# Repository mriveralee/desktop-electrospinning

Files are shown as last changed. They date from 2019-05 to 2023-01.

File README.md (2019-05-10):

# Research Code for Desktop Electrospinning

This is the research repository for `Desktop Electrospinning: A Single Extruder 3D Printer for Producing Rigid Plastic and Electrospun Textiles`. It contains the 3D printer firmware and control electronics set-up for the printer characterized in the publication  that can perform rigid plastic FDM 3D printer as well as melt electrospinning. [More information about the work can be found here](https://mikeriv.com/research/desktop-electrospinning/).

The [publication is also freely available here](https://mikeriv.com/assets/research/desktop-electrospinning/chi19-desktop-electrospinning.pdf).

  **NOTE: THIS PROJECT INVOLVES HIGH VOLTAGE -- BE AWARE AND USE AT YOUR OWN RISK!**
 

## 3D Printer Firmware and Control Electronics Set-up
This 3D printer uses a modified version of the Repeiter Firmware (v0.92) that includes add-ons for controlling high voltage via an infared signal. It also include firmware for two slave Arduino Nanos. One receives a high/low voltage signal from the 3D printer and sends out a corresponding an IR signal; the other Nano receives the IR signal and triggers a mechanical servo to open/close a connection to the high voltage ground on the 3D printer's build plate as well as toggle a solid-state relay that is connected to the high voltage power supply's AC-to-DC power adapter as shown in the simplified diagram below:

3D printer and melt electrospinning setup

## Hardware List
- High Voltage Power Supply, HV350REG(+), 5-35kV up to 1mA Positive (+) x 1 - [From Amazing1 Output](https://www.amazing1.com/hv-dc-power-supplies.html)
- Arduino Nano x 2 - [From Amazon](https://www.amazon.com/LAFVIN-Board-ATmega328P-Micro-Controller-Arduino/dp/B07G99NNXL/)
- IR Receiver Diode - can use [TSOP38238](https://www.sparkfun.com/products/10266)
- IR LED 950nm x 1 - [From Sparkfun](https://www.sparkfun.com/products/9349) 
- Servo S90 x 1 - [From Amazon](https://www.amazon.com/SunFounder-Digital-Helicopter-Fix-Wing-Airplane/dp/B01KZKOIZC/)
- Solid State Relay, 40A (3-32V DC Input) x 1 - [From Sparkfun](https://www.sparkfun.com/products/13015)
- Resistors - [From Amazon](https://www.amazon.com/AUSTOR-Resistors-Assortment-Resistor-Experiments/dp/B07BKRS4QZ/)
  - 330 Ohm Resistor x 1  
  - 470 Ohm Resistor x 3
- Servo - [From Amazon](https://www.amazon.com/SunFounder-Digital-Helicopter-Fix-Wing-Airplane/dp/B01KZKOIZC/)

The necessary electrical connections are shown in the circuit schematics below.

### IR Servo Switch Schematic
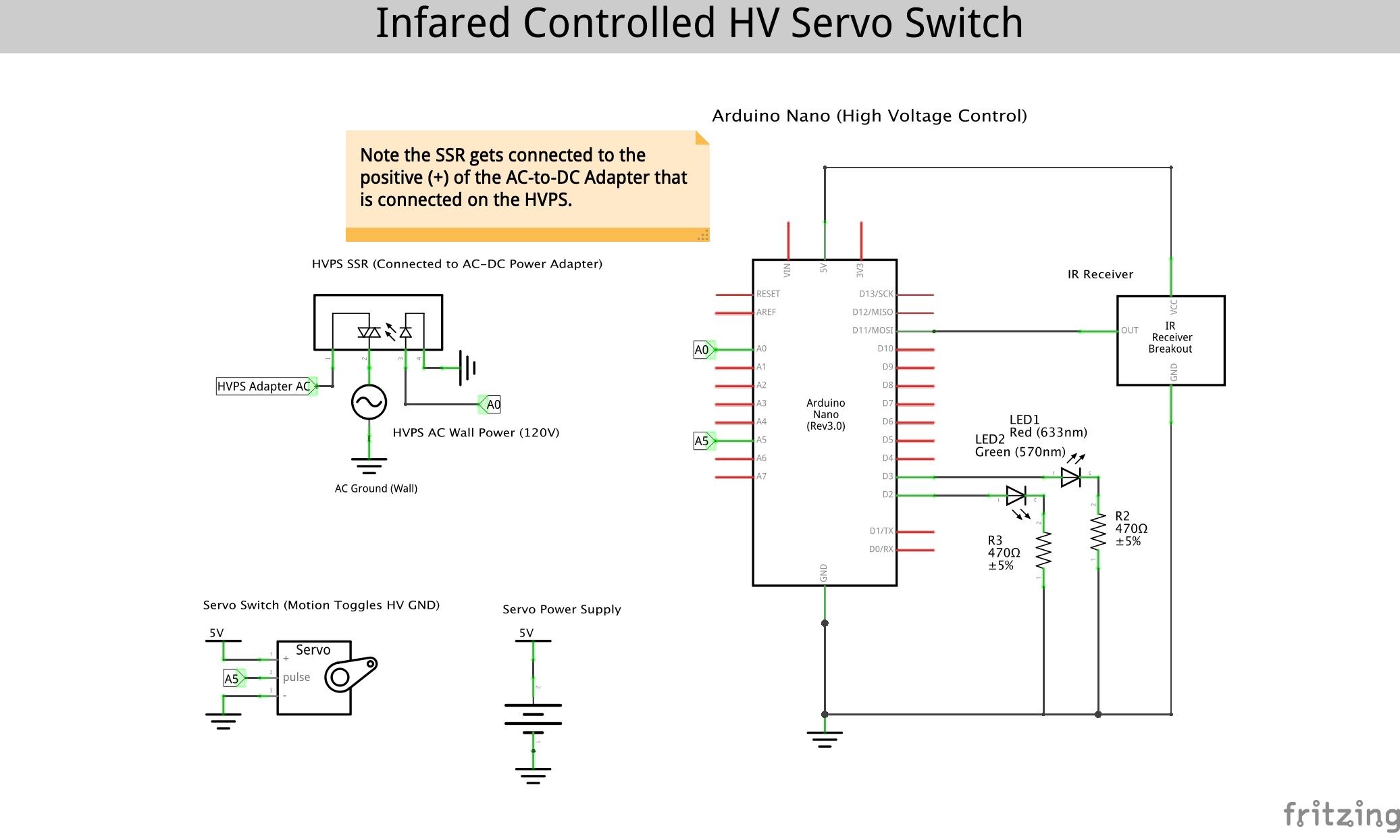
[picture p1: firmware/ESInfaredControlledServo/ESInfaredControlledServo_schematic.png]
irservo_schematic


### 3D Printer Slave IR Sender
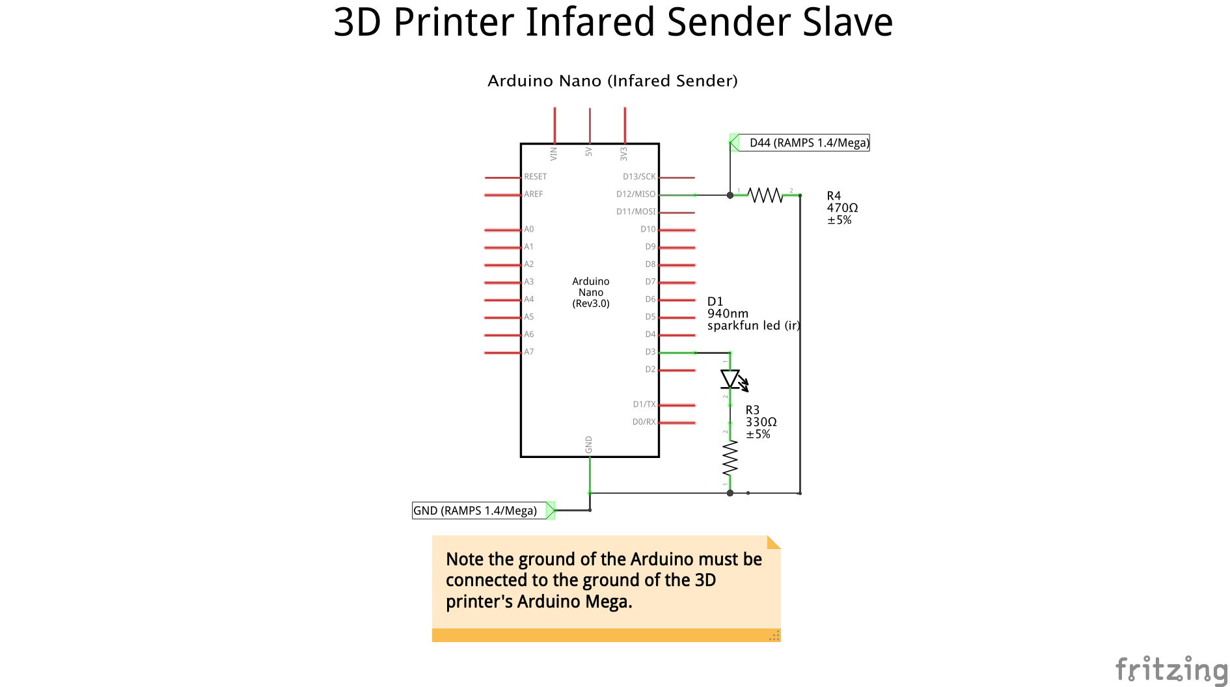
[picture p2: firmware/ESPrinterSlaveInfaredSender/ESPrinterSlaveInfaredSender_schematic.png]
irsender_schematic

Note: [RAMPS 1.4/Arduino Mega Pin out diagram can be found here](http://makerdev.com/blog/wp-content/uploads/2014/02/ramps_fanboard_annotations.jpg).

## Citation
Michael L. Rivera and Scott E. Hudson. 2019. Desktop Electrospinning: A Single Extruder 3D Printer for Producing Rigid Plastic and Electrospun Textiles. In CHI Conference on Human Factors in Computing Systems Proceedings (CHI 2019), May 4–9, 2019, Glasgow, Scotland UK. ACM, New York, NY, USA, 12 pages. https://doi.org/10.1145/3290605.3300434

# License
```MIT License

Copyright (c) 2018 Michael Rivera

Permission is hereby granted, free of charge, to any person obtaining a copy
of this software and associated documentation files (the "Software"), to deal
in the Software without restriction, including without limitation the rights
to use, copy, modify, merge, publish, distribute, sublicense, and/or sell
copies of the Software, and to permit persons to whom the Software is
furnished to do so, subject to the following conditions:

The above copyright notice and this permission notice shall be included in all
copies or substantial portions of the Software.

THE SOFTWARE IS PROVIDED "AS IS", WITHOUT WARRANTY OF ANY KIND, EXPRESS OR
IMPLIED, INCLUDING BUT NOT LIMITED TO THE WARRANTIES OF MERCHANTABILITY,
FITNESS FOR A PARTICULAR PURPOSE AND NONINFRINGEMENT. IN NO EVENT SHALL THE
AUTHORS OR COPYRIGHT HOLDERS BE LIABLE FOR ANY CLAIM, DAMAGES OR OTHER
LIABILITY, WHETHER IN AN ACTION OF CONTRACT, TORT OR OTHERWISE, ARISING FROM,
OUT OF OR IN CONNECTION WITH THE SOFTWARE OR THE USE OR OTHER DEALINGS IN THE
SOFTWARE.
```

[irservo_schematic]: https://github.com/mriveralee/desktop-electrospinning/blob/master/firmware/ESInfaredControlledServo/ESInfaredControlledServo_schematic.png "Infared Controlled Servo Circuit Schematic"

[irsender_schematic]: https://github.com/mriveralee/desktop-electrospinning/blob/master/firmware/ESPrinterSlaveInfaredSender/ESPrinterSlaveInfaredSender_schematic.png "3D Printer Slave Infared Sender Circuit Schematic"

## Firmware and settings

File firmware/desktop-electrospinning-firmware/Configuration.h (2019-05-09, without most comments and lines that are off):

#define CONFIGURATION_H
#define NUM_EXTRUDER 3
#define MOTHERBOARD 33
#include "pins.h"
#include "ESConfiguration.h"
#undef FAN_PIN
#define FAN_PIN -1
#undef FAN_BOARD_PIN
#define FAN_BOARD_PIN -1
#define BOARD_FAN_SPEED 255
#define FAN_THERMO_PIN -1
#define FAN_THERMO_MIN_PWM 128
#define FAN_THERMO_MAX_PWM 255
#define FAN_THERMO_MIN_TEMP 45
#define FAN_THERMO_MAX_TEMP 60
#define FAN_THERMO_THERMISTOR_PIN -1
#define FAN_THERMO_THERMISTOR_TYPE 1
#define BLUETOOTH_SERIAL  -1
#define BLUETOOTH_BAUD  115200
#define MIXING_EXTRUDER 0
#define DRIVE_SYSTEM 0
#define XAXIS_STEPS_PER_MM 80
#define YAXIS_STEPS_PER_MM 80
#define ZAXIS_STEPS_PER_MM 2581
#define EXTRUDER_FAN_COOL_TEMP 50
#define PDM_FOR_EXTRUDER 0
#define PDM_FOR_COOLER 0
#ifdef SUPPORT_ELECTROSPINNING
  #define DECOUPLING_TEST_MAX_HOLD_VARIANCE 20
  #define DECOUPLING_TEST_MIN_TEMP_RISE 1
  #define TEMP_DECOUPLING_TEST_INTERVAL 10000   // 10 seconds
#else
  #define DECOUPLING_TEST_MAX_HOLD_VARIANCE 20
  #define DECOUPLING_TEST_MIN_TEMP_RISE 1
  #define TEMP_DECOUPLING_TEST_INTERVAL 1000
#endif
#define KILL_IF_SENSOR_DEFECT 0
#define RETRACT_ON_PAUSE 2
#define PAUSE_START_COMMANDS ""
#define PAUSE_END_COMMANDS ""
#define EXT0_X_OFFSET ES_CONDUCTIVE_EXTRUDER_OFFSET_X_IN_MM * XAXIS_STEPS_PER_MM
#define EXT0_Y_OFFSET ES_CONDUCTIVE_EXTRUDER_OFFSET_Y_IN_MM * YAXIS_STEPS_PER_MM
#define EXT0_Z_OFFSET 0
#define EXT0_STEPS_PER_MM 92 //184
#define EXT0_TEMPSENSOR_TYPE TEMP_TYPE_NTC3950_100K  // 14 is NTC 3950 100k ; // 8 is E3D Semitech 104GT2 // 1 is just default
#define EXT0_TEMPSENSOR_PIN TEMP_0_PIN
#define EXT0_HEATER_PIN HEATER_0_PIN
#define EXT0_STEP_PIN ORIG_E1_STEP_PIN
#define EXT0_DIR_PIN ORIG_E1_DIR_PIN
#define EXT0_INVERSE 1
#define EXT0_ENABLE_PIN ORIG_E1_ENABLE_PIN
#define EXT0_ENABLE_ON 0
#define EXT0_MIRROR_STEPPER 0
#define EXT0_STEP2_PIN ORIG_E1_STEP_PIN
#define EXT0_DIR2_PIN ORIG_E1_DIR_PIN
#define EXT0_INVERSE2 0
#define EXT0_ENABLE2_PIN ORIG_E1_ENABLE_PIN
#define EXT0_MAX_FEEDRATE 50
#define EXT0_MAX_START_FEEDRATE 20
#define EXT0_MAX_ACCELERATION 5000
#define EXT0_HEAT_MANAGER 3
#define EXT0_WATCHPERIOD 1
#define EXT0_PID_INTEGRAL_DRIVE_MAX 245
#define EXT0_PID_INTEGRAL_DRIVE_MIN 40
#define EXT0_PID_PGAIN_OR_DEAD_TIME 7
#define EXT0_PID_I 2
#define EXT0_PID_D 40
#define EXT0_PID_MAX 255
#define EXT0_ADVANCE_K 0
#define EXT0_ADVANCE_L 0
#define EXT0_ADVANCE_BACKLASH_STEPS 0
#define EXT0_WAIT_RETRACT_TEMP 150
#define EXT0_WAIT_RETRACT_UNITS 0
#define EXT0_SELECT_COMMANDS ""
#define EXT0_DESELECT_COMMANDS ""
#define EXT0_EXTRUDER_COOLER_PIN -1
#define EXT0_EXTRUDER_COOLER_SPEED 255
#define EXT0_DECOUPLE_TEST_PERIOD 20000
#define EXT0_JAM_PIN -1
#define EXT0_JAM_PULLUP 0
#define EXT1_X_OFFSET 0
#define EXT1_Y_OFFSET 0
#define EXT1_Z_OFFSET 0
#ifdef SUPPORT_ELECTROSPINNING
  #define SHARED_EXTRUDER_HEATER ES_SHARED_HEATER_E1_AND_E2 // Sharing the heater with our two extruders for ES and PLA
  #define EXT1_TEMPSENSOR_TYPE ES_TEMP_TYPE   // 1
  #define EXT1_TEMPSENSOR_PIN  ES_TEMP_PIN    // TEMP_0_PIN
  #define EXT1_STEPS_PER_MM  ES_EXTRUDER_NORMAL_STEPS_PER_MM
  #define EXT1_HEATER_PIN ES_HEATER_PIN
#else
  #define SHARED_EXTRUDER_HEATER 0
  #define EXT1_TEMPSENSOR_TYPE 14
  #define EXT1_TEMPSENSOR_PIN  TEMP_0_PIN
  #define EXT1_HEATER_PIN HEATER_0_PIN
  #define EXT1_STEPS_PER_MM  92
#endif
#define EXT1_STEP_PIN ORIG_E0_STEP_PIN
#define EXT1_DIR_PIN ORIG_E0_DIR_PIN
#define EXT1_INVERSE 0
#define EXT1_ENABLE_PIN ORIG_E0_ENABLE_PIN
#define EXT1_ENABLE_ON 0
#define EXT1_MIRROR_STEPPER 0
#define EXT1_STEP2_PIN ORIG_E0_STEP_PIN
#define EXT1_DIR2_PIN ORIG_E0_DIR_PIN
#define EXT1_INVERSE2 0
#define EXT1_ENABLE2_PIN ORIG_E0_ENABLE_PIN
#define EXT1_MAX_FEEDRATE 50
#define EXT1_MAX_START_FEEDRATE 20
#define EXT1_MAX_ACCELERATION 5000
#define EXT1_HEAT_MANAGER 3
#define EXT1_WATCHPERIOD 1
#ifdef SUPPORT_ELECTROSPINNING
  #define EXT1_PID_INTEGRAL_DRIVE_MAX ES_PID_INTEGRAL_DRIVE_MAX
  #define EXT1_PID_INTEGRAL_DRIVE_MIN 40
  #define EXT1_PID_PGAIN_OR_DEAD_TIME ES_PID_PGAIN_OR_DEAD_TIME
  #define EXT1_PID_I ES_PID_I
  #define EXT1_PID_D ES_PID_D
  #define EXT1_PID_MAX 255
  #define EXT1_ADVANCE_K 0
  #define EXT1_ADVANCE_L 0
#else
  #define EXT1_PID_INTEGRAL_DRIVE_MAX 230
  #define EXT1_PID_INTEGRAL_DRIVE_MIN 40
  #define EXT1_PID_PGAIN_OR_DEAD_TIME 9.51
  #define EXT1_PID_I 2
  #define EXT1_PID_D 40
  #define EXT1_PID_MAX 255
  #define EXT1_ADVANCE_K 0
  #define EXT1_ADVANCE_L 0
#endif
#define EXT1_ADVANCE_BACKLASH_STEPS 0
#define EXT1_WAIT_RETRACT_TEMP 150
#define EXT1_WAIT_RETRACT_UNITS 0
#define EXT1_SELECT_COMMANDS ""
#define EXT1_DESELECT_COMMANDS ""
#define EXT1_EXTRUDER_COOLER_PIN -1
#define EXT1_EXTRUDER_COOLER_SPEED 255
#ifdef SUPPORT_ELECTROSPINNING
#define EXT1_DECOUPLE_TEST_PERIOD ES_DECOUPLE_TEST_PERIOD
#else
#define EXT1_DECOUPLE_TEST_PERIOD 20000
#endif
#define EXT1_JAM_PIN -1
#define EXT1_JAM_PULLUP 0
#ifdef SUPPORT_ELECTROSPINNING
#define EXT2_X_OFFSET ES_EXTRUDER_X_OFFSET_MM * XAXIS_STEPS_PER_MM
#define EXT2_Y_OFFSET 0
#define EXT2_Z_OFFSET 0
#define EXT2_STEPS_PER_MM ES_EXTRUDER_SPIN_STEPS_PER_MM
#define EXT2_TEMPSENSOR_TYPE ES_TEMP_TYPE
#define EXT2_TEMPSENSOR_PIN  ES_TEMP_PIN
#define EXT2_HEATER_PIN -1 // Important for sharing heater
#define EXT2_STEP_PIN ORIG_E0_STEP_PIN
#define EXT2_DIR_PIN ORIG_E0_DIR_PIN
#define EXT2_INVERSE 0
#define EXT2_ENABLE_PIN ORIG_E0_ENABLE_PIN
#define EXT2_ENABLE_ON 0
#define EXT2_MIRROR_STEPPER 0
#define EXT2_STEP2_PIN ORIG_E0_STEP_PIN
#define EXT2_DIR2_PIN ORIG_E0_DIR_PIN
#define EXT2_INVERSE2 0
#define EXT2_ENABLE2_PIN ORIG_E0_ENABLE_PIN
#define EXT2_MAX_FEEDRATE ES_EXTRUDER_SPIN_MAX_FEEDRATE
#define EXT2_MAX_START_FEEDRATE ES_EXTRUDER_SPIN_MAX_START_FEEDRATE
#define EXT2_MAX_ACCELERATION ES_EXTRUDER_SPIN_MAX_ACCELERATION
#else
#define EXT2_X_OFFSET 0
#define EXT2_Y_OFFSET 0
#define EXT2_Z_OFFSET 0
#define EXT2_STEPS_PER_MM 92
#define EXT2_TEMPSENSOR_TYPE 1
#define EXT2_TEMPSENSOR_PIN TEMP_2_PIN
#define EXT2_HEATER_PIN HEATER_1_PIN
#define EXT2_STEP_PIN ORIG_E1_STEP_PIN
#define EXT2_DIR_PIN ORIG_E1_DIR_PIN
#define EXT2_INVERSE 1
#define EXT2_ENABLE_PIN ORIG_E1_ENABLE_PIN
#define EXT2_ENABLE_ON 0
#define EXT2_MIRROR_STEPPER 0
#define EXT2_STEP2_PIN ORIG_E1_STEP_PIN
#define EXT2_DIR2_PIN ORIG_E1_DIR_PIN
#define EXT2_INVERSE2 0
#define EXT2_ENABLE2_PIN ORIG_E1_ENABLE_PIN
#define EXT2_MAX_FEEDRATE 50
#define EXT2_MAX_START_FEEDRATE 20
#define EXT2_MAX_ACCELERATION 5000
#endif
#define EXT2_HEAT_MANAGER 3
#define EXT2_WATCHPERIOD 1
#ifdef SUPPORT_ELECTROSPINNING
#define EXT2_PID_INTEGRAL_DRIVE_MAX ES_PID_INTEGRAL_DRIVE_MAX
#define EXT2_PID_INTEGRAL_DRIVE_MIN 40
#define EXT2_PID_PGAIN_OR_DEAD_TIME ES_PID_PGAIN_OR_DEAD_TIME
#define EXT2_PID_I ES_PID_I
#define EXT2_PID_D ES_PID_D
#define EXT2_PID_MAX 255
#define EXT2_ADVANCE_K 0
#define EXT2_ADVANCE_L 0
#else
#define EXT2_PID_INTEGRAL_DRIVE_MAX 230
#define EXT2_PID_INTEGRAL_DRIVE_MIN 40
#define EXT2_PID_PGAIN_OR_DEAD_TIME 7
#define EXT2_PID_I 1.60
#define EXT2_PID_D 14.09
#define EXT2_PID_MAX 255
#define EXT2_ADVANCE_K 0
#define EXT2_ADVANCE_L 0
#endif
#define EXT2_ADVANCE_BACKLASH_STEPS 0
#define EXT2_WAIT_RETRACT_TEMP 150
#define EXT2_WAIT_RETRACT_UNITS 0
#define EXT2_SELECT_COMMANDS ""
#define EXT2_DESELECT_COMMANDS ""
#define EXT2_EXTRUDER_COOLER_PIN -1
#define EXT2_EXTRUDER_COOLER_SPEED 255
#ifdef SUPPORT_ELECTROSPINNING
  #define EXT2_DECOUPLE_TEST_PERIOD ES_DECOUPLE_TEST_PERIOD
#else
  #define EXT2_DECOUPLE_TEST_PERIOD 12000
#endif
#define EXT2_JAM_PIN -1
#define EXT2_JAM_PULLUP 0
#define FEATURE_RETRACTION 0
#define AUTORETRACT_ENABLED 0
#define RETRACTION_LENGTH 3
#define RETRACTION_LONG_LENGTH 13
#define RETRACTION_SPEED 40
#define RETRACTION_Z_LIFT 0
#define RETRACTION_UNDO_EXTRA_LENGTH 0
#define RETRACTION_UNDO_EXTRA_LONG_LENGTH 0
#define RETRACTION_UNDO_SPEED 20
#define FILAMENTCHANGE_X_POS 0
#define FILAMENTCHANGE_Y_POS 0
#define FILAMENTCHANGE_Z_ADD  2
#define FILAMENTCHANGE_REHOME 1
#define FILAMENTCHANGE_SHORTRETRACT 5
#define FILAMENTCHANGE_LONGRETRACT 50
#define JAM_STEPS 220
#define JAM_SLOWDOWN_STEPS 320
#define JAM_SLOWDOWN_TO 70
#define JAM_ERROR_STEPS 500
#define JAM_MIN_STEPS 10
#define JAM_ACTION 1
#define RETRACT_DURING_HEATUP true
#define PID_CONTROL_RANGE 20
#define SKIP_M109_IF_WITHIN 2
#define SCALE_PID_TO_MAX 0
#define TEMP_HYSTERESIS 0
#define EXTRUDE_MAXLENGTH 160
#define NUM_TEMPS_USERTHERMISTOR0 0
#define USER_THERMISTORTABLE0 {}
#define NUM_TEMPS_USERTHERMISTOR1 0
#define USER_THERMISTORTABLE1 {}
#define NUM_TEMPS_USERTHERMISTOR2 0
#define USER_THERMISTORTABLE2 {}
#define GENERIC_THERM_VREF 5
#define GENERIC_THERM_NUM_ENTRIES 33
#define HEATER_PWM_SPEED 0
#define HAVE_HEATED_BED 0
#define HEATED_BED_MAX_TEMP 120
#define SKIP_M190_IF_WITHIN 3
#define HEATED_BED_SENSOR_TYPE 1
#define HEATED_BED_SENSOR_PIN TEMP_1_PIN
#define HEATED_BED_HEATER_PIN HEATER_1_PIN
#define HEATED_BED_SET_INTERVAL 5000
#define HEATED_BED_HEAT_MANAGER 0
#define HEATED_BED_PID_INTEGRAL_DRIVE_MAX 255
#define HEATED_BED_PID_INTEGRAL_DRIVE_MIN 80
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

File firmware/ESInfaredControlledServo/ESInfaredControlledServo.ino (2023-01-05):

#include <ir_Lego_PF_BitStreamEncoder.h>
#include <boarddefs.h>
#include <IRremoteInt.h>
#include <IRremote.h>

#include <Servo.h>

/*
   This sketch received and IRSignal send from an IR LED, 
   then triggers a servo to rotate based on the signal 
   This sketch uses Ken Shirriff's *aweesome* IRremote library:
       https://github.com/shirriff/Arduino-IRremot
   Hardware setup:
     * The output of an IR Receiver Diode (38 kHz demodulating
       version) should be connected to the Arduino's pin 11.
       * The IR Receiver diode should also be powered off the
         Arduino's 5V and GND rails.
*/

/* Define the IR remote button codes. We're only using the
   least signinficant two bytes of these codes. Each one 
   should actually have 0x10EF in front of it. */
const uint16_t BUTTON_PREFIX = 0x10EF;
const uint16_t BUTTON_A = 0xF807;
const uint16_t BUTTON_CIRCLE = 0x20DF;

#define SEND_CODE_BUTTON_CIRCLE 0x10EF20DF
#define SEND_CODE_BUTTON_A 0x10EFF807

/* Connect the output of the IR receiver diode to pin 11. */
int RECV_PIN = 11;

/* Initialize the IR_RECEIVER part of the IRremote  library */
IRrecv IR_RECEIVER(RECV_PIN);
decode_results RECEIVED_RESULTS; // This will store our IR received codes

/* Vars for the Received IR Code */
unsigned int RECEIVED_IR_BUFFER[RAWBUF];// = {BUTTON_PREFIX, BUTTON_CIRCLE}; // Storage for raw (UNKNOWN) codes
boolean WAS_CODE_RECEIVED  = true; // A boolean to keep track of if a code was received
unsigned int RECEIVED_CODE_LENGTH  = 2; // The length of the code
int RECEIVED_CODE_TYPE = NEC; // The type of code (NEC, SONY, UNKNOWN, etc.)
unsigned int RECEIVED_CODE_VALUE  = BUTTON_CIRCLE; // The value of a known code
uint16_t LAST_RECEIVED_CODE = 0; // This keeps track of the last code RX'd
long LAST_IR_RECEIVED_TIMESTAMP = 0; // timestamp from the last ir signal we decoded 


// Set-up for the servo
Servo HV_SERVO_SWITCH;  // create servo object to control a servo
const int HV_SERVO_SWITCH_PIN = A5;   // Servo pin
const int ES_HV_SERVO_STATE_ON = 30; 
const int  ES_HV_SERVO_STATE_GROUNDED = 0;

const int HV_SSR_SWITCH_PIN = A0;         // Solid-state-relay pin

bool IS_HV_ENABLED = false;               // State of HV

// Set-up for the LED Status Pin
const int IR_STATUS_LED_PIN = 3;          // LED to show if IR is being received
const int HV_ENABLED_STATUS_LED_PIN = 2;  // LED to show if HV is on

// IR related
bool IS_IR_RECEIVING = false;
int IR_STATUS_RECEIVING_TIME_DELAY = 100;
long LAST_IR_STATUS_LED_TIME = 0;
long IR_RECEIVING_TIMEOUT_FAILSAFE = 300;


void setup() {
  Serial.begin(9600);
  pinMode(IR_STATUS_LED_PIN, OUTPUT);
  pinMode(HV_ENABLED_STATUS_LED_PIN, OUTPUT);
  pinMode(HV_SSR_SWITCH_PIN, OUTPUT);
  HV_SERVO_SWITCH.attach(HV_SERVO_SWITCH_PIN);
  updateHVServoState();
  updateStatusLEDState();
  IR_RECEIVER.enableIRIn(); // Start the receiver
}


// loop() checks for a received IR code.
void loop() {
  if (IR_RECEIVER.decode(&RECEIVED_RESULTS)) {
    updateIRReceive(); // Sort out the received code
    WAS_CODE_RECEIVED  = true;
    // Do stuff with the code
     /* read the RX'd IR into a 16-bit variable: */
    uint16_t resultCode = (RECEIVED_RESULTS.value & 0xFFFF);

    /* The remote will continue to spit out 0xFFFFFFFF if a 
     button is held down. If we get 0xFFFFFFF, let's just
     assume the previously pressed button is being held down */
    if (resultCode == 0xFFFF) {
      resultCode = LAST_RECEIVED_CODE;
    } else {
      LAST_RECEIVED_CODE = resultCode;
    }

    // This switch statement checks the received IR code against
    // all of the known codes. Each button press produces a 
    // serial output, and has an effect on the LED output.
    switch (resultCode) {
      case BUTTON_CIRCLE:        
        IS_HV_ENABLED = true;
        Serial.println("Circle");
        break;
      case BUTTON_A:
        IS_HV_ENABLED = false;
        Serial.println("A");
        break;
      default:
        Serial.print("Unrecognized code received: 0x");
        Serial.println(RECEIVED_RESULTS.value, HEX);
        // Return to OFF_STATE
        break;        
    }
    // Toggle IR LED Status
    if (IS_IR_RECEIVING) {
          IS_IR_RECEIVING = false;
    } else {
      IS_IR_RECEIVING = true; // Flip IS_IR_RECEIVING
    } 
    IR_RECEIVER.resume(); // re-enable receive 
    LAST_IR_RECEIVED_TIMESTAMP = millis();  // track when we last received a decodeable ir signal
  } 
  
  if (millis() - LAST_IR_RECEIVED_TIMESTAMP >= IR_RECEIVING_TIMEOUT_FAILSAFE) {
    IS_HV_ENABLED = false;
  }
  updateStatusLEDState();
  updateHVServoState();
  updateHVSSRState();
}


void updateIRReceive() {
  RECEIVED_CODE_TYPE = RECEIVED_RESULTS.decode_type;
  RECEIVED_CODE_LENGTH = RECEIVED_RESULTS.rawlen;
  if (RECEIVED_CODE_TYPE == NEC) {
    Serial.print("Received NEC: ");
    if (RECEIVED_RESULTS.value == REPEAT) {
      // Don't record a NEC repeat value as that's useless.
      Serial.println("repeat.");
      //return;
    }
  } 
  Serial.println(RECEIVED_RESULTS.value, HEX);
  RECEIVED_CODE_VALUE = RECEIVED_RESULTS.value;
  RECEIVED_CODE_LENGTH = RECEIVED_RESULTS.bits;
}


void updateHVServoState() {
  if (IS_HV_ENABLED) { 
     HV_SERVO_SWITCH.write(ES_HV_SERVO_STATE_ON);
      Serial.println("HV ON");
  } else {
      HV_SERVO_SWITCH.write(ES_HV_SERVO_STATE_GROUNDED);
      Serial.println("HV OFF");
  }
  delay(15);
}

void updateHVSSRState() {
  digitalWrite(HV_SSR_SWITCH_PIN, IS_HV_ENABLED ? HIGH : LOW);
}

void updateStatusLEDState() {
  if (millis() - LAST_IR_STATUS_LED_TIME  >= IR_STATUS_RECEIVING_TIME_DELAY) {
    digitalWrite(IR_STATUS_LED_PIN, IS_IR_RECEIVING ? HIGH : LOW);
    LAST_IR_STATUS_LED_TIME = millis();
  }
  digitalWrite(HV_ENABLED_STATUS_LED_PIN, IS_HV_ENABLED ? HIGH : LOW);
}

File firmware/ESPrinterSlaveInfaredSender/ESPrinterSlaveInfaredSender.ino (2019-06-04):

#include <ir_Lego_PF_BitStreamEncoder.h>
#include <boarddefs.h>
#include <IRremoteInt.h>
#include <IRremote.h>

/* ESPrinterSlaveInfaredSender
   This sketch uses Ken Shirriff's *awesome* IRremote library:
       https://github.com/shirriff/Arduino-IRremote

    This sketch sends an one IR code out of an attached IR LED on pin 3,
    when the voltage on pin 12 is set to high; and another when the voltage is set to low

   Hardware setup:
     * The anode (+, longer leg) of an IR LED should be connected to pin 3 of 
       the Arduino. The cathode (-) should be connected to a 330
       Ohm resistor, which connects to ground.
     * A Wire connecting D44 of a RAMPS 1.4/Mega 3D printer controller should be connected 
     * to pin 12 of this arduino with a current-limiting resistor (470ohm) in between.

*/

/* Define the IR remote button codes. We're only using the
   least signinficant two bytes of these codes. Each one 
   should actually have 0x10EF in front of it. Find these codes
   by running the IRrecvDump example sketch included with
   the IRremote library.*/
//const uint16_t BUTTON_PREFIX = 0x10EF;
//const uint16_t BUTTON_A = 0xF807;      
//const uint16_t BUTTON_CIRCLE = 0x20DF;  

#define SEND_CODE_BUTTON_CIRCLE 0x10EF20DF    // Code for HV ON 
#define SEND_CODE_BUTTON_A 0x10EFF807         // Code for HV OFF

/* Storage variables for the send IR code: */
// The length of the header we send for NEC
unsigned int NEC_HEADER_LENGTH = 16;

// The length of the code in bytes
unsigned int SEND_CODE_LENGTH  = 16; 

// The code we send for the ESP set up
int SEND_CODE_TYPE = NEC;

// Timing Vars
long SEND_TIME_DELAY = 40;
long LAST_SEND_IR_TIME = 0;

const int TRIGGER_SEND_IR_STATUS_PIN = 12;  // Status pin connected to the 3D Printer 
boolean IS_HV_ENABLED = false;

// Enables IR transmit on pin 3
IRsend IR_SENDER; 

// setup() initializes serial and the Infrared receiver.
void setup() {
  // Init the status pin
  pinMode(TRIGGER_SEND_IR_STATUS_PIN, INPUT); 
  Serial.begin(9600);
}


// loop() checks for either a button press or a received IR code.
void loop() {
  // Check if status pin is high
  IS_HV_ENABLED = (digitalRead(TRIGGER_SEND_IR_STATUS_PIN) == HIGH) 
    ? true 
    : false;
   // If hv is enabled we send the Enable symbol
  if (!IS_HV_ENABLED) {
    sendCode(SEND_CODE_TYPE, SEND_CODE_BUTTON_A, NEC_HEADER_LENGTH + SEND_CODE_LENGTH); 
  } else {
    sendCode(SEND_CODE_TYPE, SEND_CODE_BUTTON_CIRCLE, NEC_HEADER_LENGTH + SEND_CODE_LENGTH); 
  }
  delay(SEND_TIME_DELAY);
  LAST_SEND_IR_TIME = millis();
}

void sendCode(int codeType, unsigned int codeToSend, int lenOfIR) {
  if (codeType == NEC) {
    IR_SENDER.sendNEC(codeToSend, lenOfIR);
    Serial.print("Sent NEC ");
    Serial.println(codeToSend, HEX);
  }
}

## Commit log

2019-05-09 Initial firmware version
    [Configuration.h, ESInfaredControlledServo.fzz, ESPrinterSlaveInfaredSender.fzz]
2019-06-04 Update schematics and some firmware vars
    [ESInfaredControlledServo.fzz, ESPrinterSlaveInfaredSender.fzz]
2023-01-05 latest before clean
    [ESPrinterSlaveInfaredSenderComponent.fzz]

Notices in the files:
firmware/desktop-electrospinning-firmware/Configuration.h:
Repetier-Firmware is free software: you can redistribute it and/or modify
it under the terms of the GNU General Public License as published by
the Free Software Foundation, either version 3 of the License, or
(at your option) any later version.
